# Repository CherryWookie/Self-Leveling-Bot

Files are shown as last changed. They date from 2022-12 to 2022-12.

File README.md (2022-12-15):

# Lab8 - Final Project (Self-Leveling Robot)
Michael Sell (Lab partner: Ben Schaser)

## Table of Contents:

[`Resources`](#resources)

[`Materials`](#materials)

[`Objective`](#objectiveproposal)

[`3D Printing/Laser Cutting`](#3d-printinglaser-cutting)

[`Robot Design`](#robot-design)

[`Robot Assembly`](#robot-assembly)

[`Code`](#code)

* [PID Control](#pid-control)

[`Troubleshooting`](#troubleshooting)

[`Performance`](#performance)

## Resources
#
* [Self-Levling Bot Instructional](https://www.instructables.com/Arduino-Self-Balancing-Robot-1/)
* [Self-Leveling Bot w/ Video](https://electricdiylab.com/diy-self-balancing-robot/)
* [MotorShield Instruction](https://learn.adafruit.com/adafruit-motor-shield-v2-for-arduino/using-stepper-motors)
* [Potential Wheel Option](https://www.amazon.com/90-10mm-Black-Robot-Wheels/dp/B00T3MQG7M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)
* [Accelstepper](https://github.com/adafruit/AccelStepper/blob/master/AccelStepper.cpp)
* [DC Motor that would probably work](https://www.studica.com/612rpm-6-12v-planetary-gearmotor)
* [Adafruit Motorshield Libray V_2](https://github.com/adafruit/Adafruit_Motor_Shield_V2_Library)

## Materials
#
* `Arduino UNO`

* `2 NEMA 17 Stepper Motors (42mm High Torque Hybrid Stepping Motor)`
    * [WEBPAGE for initial motors](https://www.adafruit.com/product/324)
    * [DataSheet][def]
    * [WEBPAGE for secondary motors](https://www.amazon.com/STEPPERONLINE-Stepper-Bipolar-Connector-compatible/dp/B00PNEQKC0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)

[def]: motordatasheet.jpeg

* `Adafruit Motorshield Kit`
    * [LINK TO WEBPAGE](https://www.adafruit.com/product/1438)
    * <a href="https://cdn-shop.adafruit.com/datasheets/TB6612FNG_datasheet_en_20121101.pdf">View DataSheet</a> 
    
* `Gyroscope Module`
    * [LINK TO WEBPAGE](https://www.amazon.com/HiLetgo-MPU-6050-Accelerometer-Gyroscope-Converter/dp/B00LP25V1A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)
    * Main Chip: MPU-6050
    * Power supply: 3~5V
    * Communication mode: standard IIC communication protocol
    * Chip built-in 16bit AD converter, 16bit data output
    * Gyroscopes range: +/- 250 500 1000 2000 degree/sec
    * Acceleration range: ±2 ±4 ±8 ±16g 

* `Batteries`
    * In our case: 8 AA 1.5V rechargeable batteries (TENERGY Premium 2500mAh Ni-MH Rechargeable)

* `Breadboard/wires`

* `Wheels/Tires`
    * Anything around 10cm diameter wheels should suffice. Preferably a good amount of grip for the the bot to maintain traction with various surfaces. In our case, we will be 3D Printing the wheel rims and using rubber tape to wrap around the rims for our "tires".
    * [STL FILE](wheel-rims.stl)

* `Hardware`
    * Various screws, nuts, etc. that we have yet to determine
    * Brackets for stepper motor installation
    * 4 support beams for structural integrity

* `Structure`
    * Platforms for UNO, battery, and anything else to rest on while offering the bot support. (3 in total, in our case, we will be cutting them out of a 1/4" piece of wood with a laser cutter)

## Objective/Proposal
#
Create a robot using an Arduino Uno and the above listed materials that is able to autonomously level itself without any human interaction after the bot is turned on.

`Steps to Completion:` We will be designing the robot similar to other bots listed under the [resources](#resources) section. We will be using all the components listed above with miscellaneous hardware in order to accomplish this. As for the software, we will be using a PID controller in order to control our robot. This will depend on our robot structure and the exact dimensions. We will be 3D printing the wheel rims and using the laser cutter in order to cut our platform sectionals. 

## Testing Components
#

We started by testing the stepper motors and followed the online instructions on the webpage for the motor shield. We soldered the shield and the gyroscope.

<p align="left">
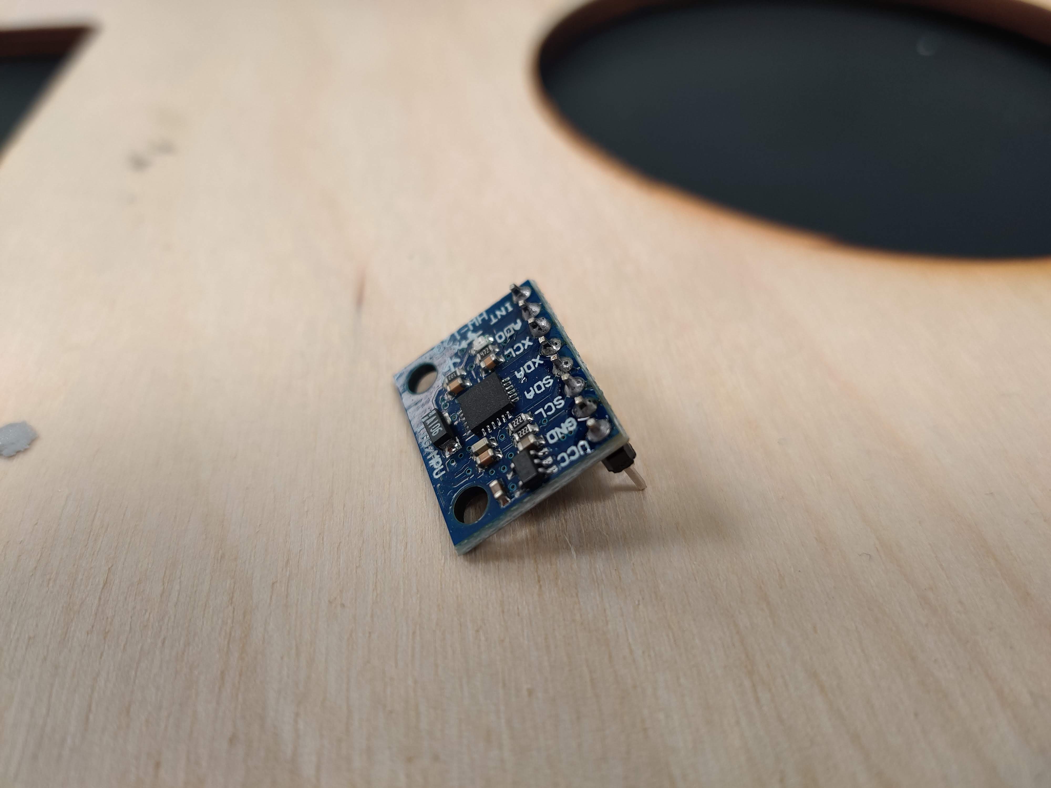
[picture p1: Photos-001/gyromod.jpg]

<align="right">
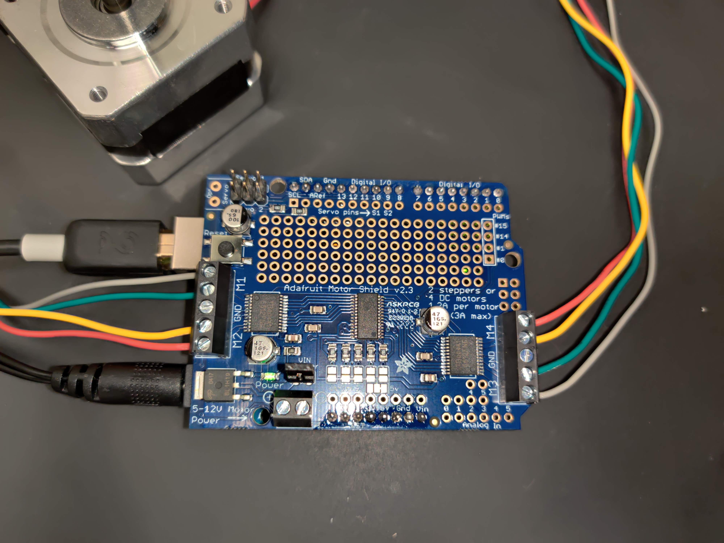
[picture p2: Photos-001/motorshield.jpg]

<align="center">
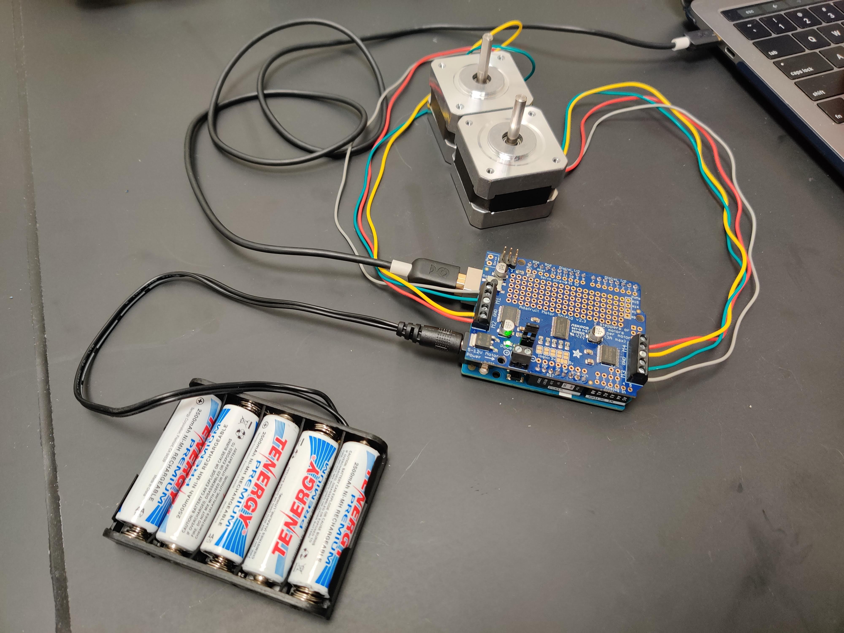
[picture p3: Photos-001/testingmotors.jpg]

</p>

We had to make sure the .h files (all the required libraries) were also in the arduino folder.

After putting the motors and the new wheels on our robot frame, we found that the motors were not making us very happy. For one, they didn't seem to be able to go fast enough. They produced very little torque and they were very jerky in motion as we have to step each one at a time instead of running them simultaneously. To remedy this, we went from the initial stepper motors and moved to our secondary stepper motors. These were rated for 2A instead of 350mA and supposedly had a higher torque at around .5NM. There is a calculation based on the weight and height of your robot to calculate how much torque is necessary for motors but we didn't do that because we were lazy. Also there weren't that many options for stepper motors so we just picked the one that could deliver the most torque without being too big. 

## 3D Printing/Laser Cutting
#

`Laser Cut thickness for red line: .072pt, Red line`

Our first test of the 3D print for the wheel rims didn't turn out very well as it printed out vertical instead of horizontal. To make it better, we switched it so that it was lying horizontal on the base plate and switched from non-soluble support material to water-soluble material so that we would end up with a cleaner product. We ended up re-printing a third time and this time opted for some larger wheels to fit our bigger robot design. 

<p align="center">
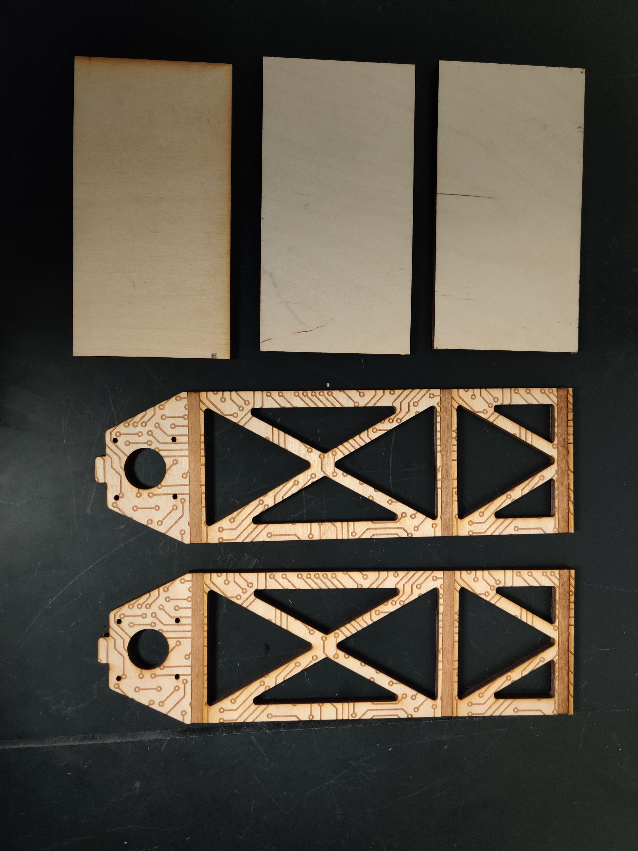
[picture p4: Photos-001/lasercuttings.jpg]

</p>

<!-- ![image](Photos-001/IMG_20221205_134104.jpg) -->
Above is the image of our laser cut components for our new design.

## Robot Design
#

Platform Dimensions: 3.5 x 7 x 1/4" (x3) (Perhaps?)
(9cm x 18cm)
8.4 cm x 16 cm

For general robot design, we started out with a rough prototype version involving a decomissioned erector set as seen below. This Mark1 was very heavy in nature due to the amount of metal used. It was also quite tall and we soon realized that we would have to look at other methods for constructing a better robot with a better weight distribution. We had thought that more weight on the top would make it easier to balance the robot, and while this may be true in theory, it ended up making the entire robot too heavy and the motors ended up not being able to move it.

<p align="left">
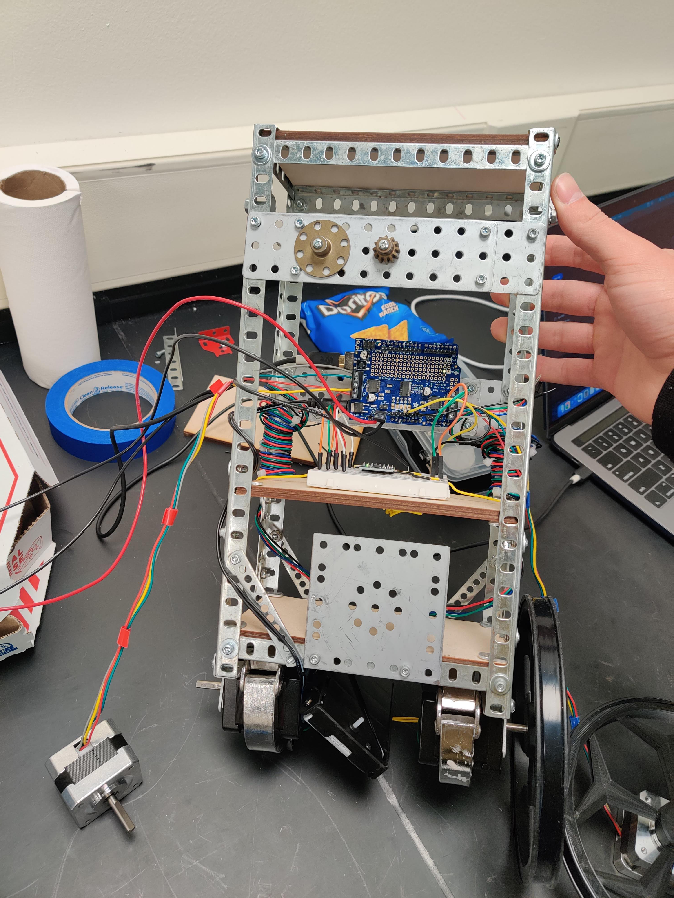
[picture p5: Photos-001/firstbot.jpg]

<align="right">
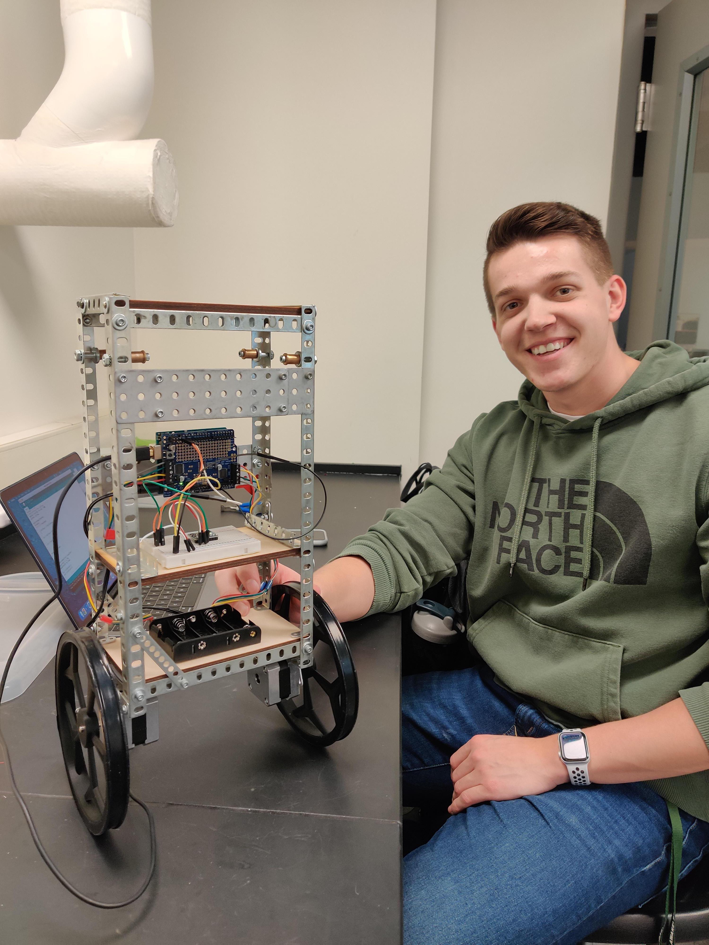
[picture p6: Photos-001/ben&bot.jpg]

</p>

Eventually, after a few days of adjusting parameters and trying different methods, we concluded the new stepper motors were still not fast enough and were not stepping in sync, causing the bot to shake violently, twist, and fall over. We then went to Dr. Kuehns laboratory and got two of his DC Planetary Gearbox motors. One of the motors he had was great with an integrated gearbox of 612RPM. This had enough speed and plenty of torque for our purposes. Unfortunately, the other gearbox was set at 60RPM and so we were unable to use them simultaneously. We purchased two more pairs of DC motors from American Science and Surplus but we quickly discovered that there was not enough torque being generated by either kind. 

We ended up completely rethinking our design as we kept running into the problem of our robot falling over too fast and the motors not having enough torque/speed to recover. We hoped that creating a chassis out of wood while making it smaller would aid in this problem. 

<p align="center">
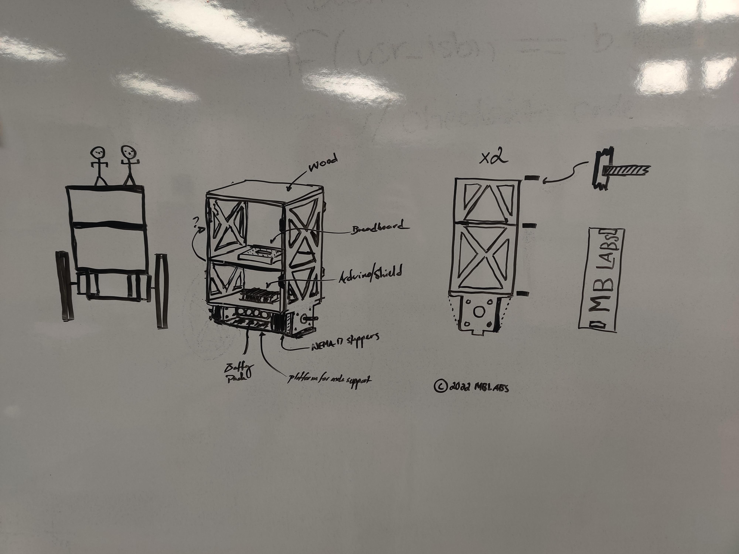
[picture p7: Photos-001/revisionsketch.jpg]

</p>

## Robot Assembly
#

`Note - Black M3 screws used to hold motors in brackets are Professor Brewsters! (Now the silver M3 screws*)`

Bonding agent used: Locktite Professional Performance Spray Adhesive (Obtained from Dr. Kuehn)

<p align="center">
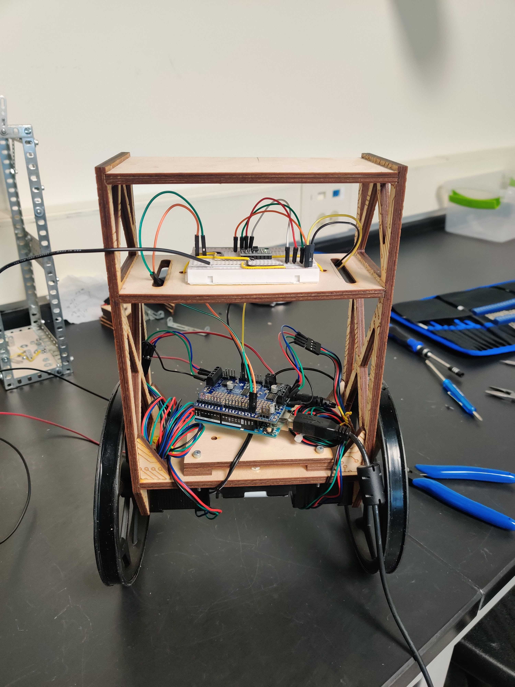
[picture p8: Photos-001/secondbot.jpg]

</p>

<p align="center">
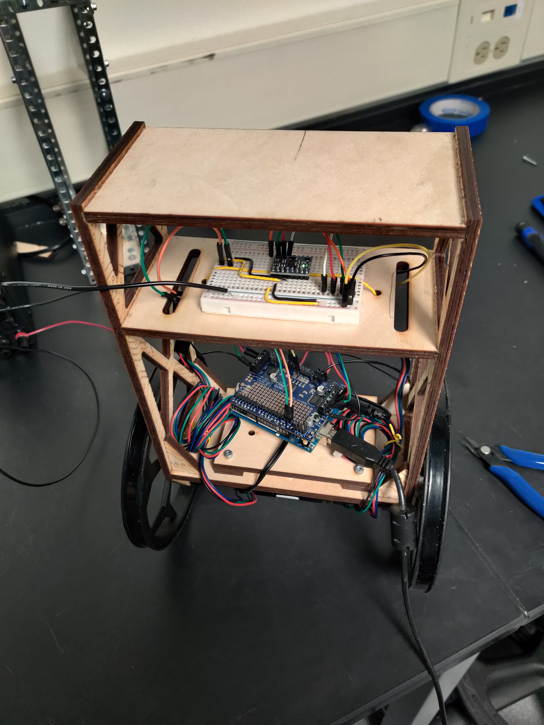
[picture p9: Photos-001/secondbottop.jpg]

</p>

After lasercutting a completely new design to accomodate our DC motors, we went back to our secondary frame and resorted to using the stepper motors. Our final design was quite good with a solid structural integrity and pleasing asthetic:

<p align="center">
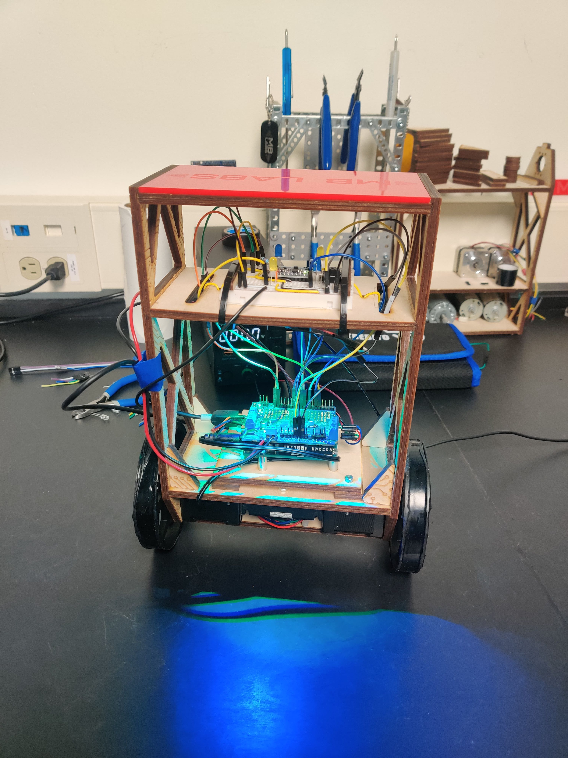
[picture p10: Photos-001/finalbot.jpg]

</p>
<p align="center">
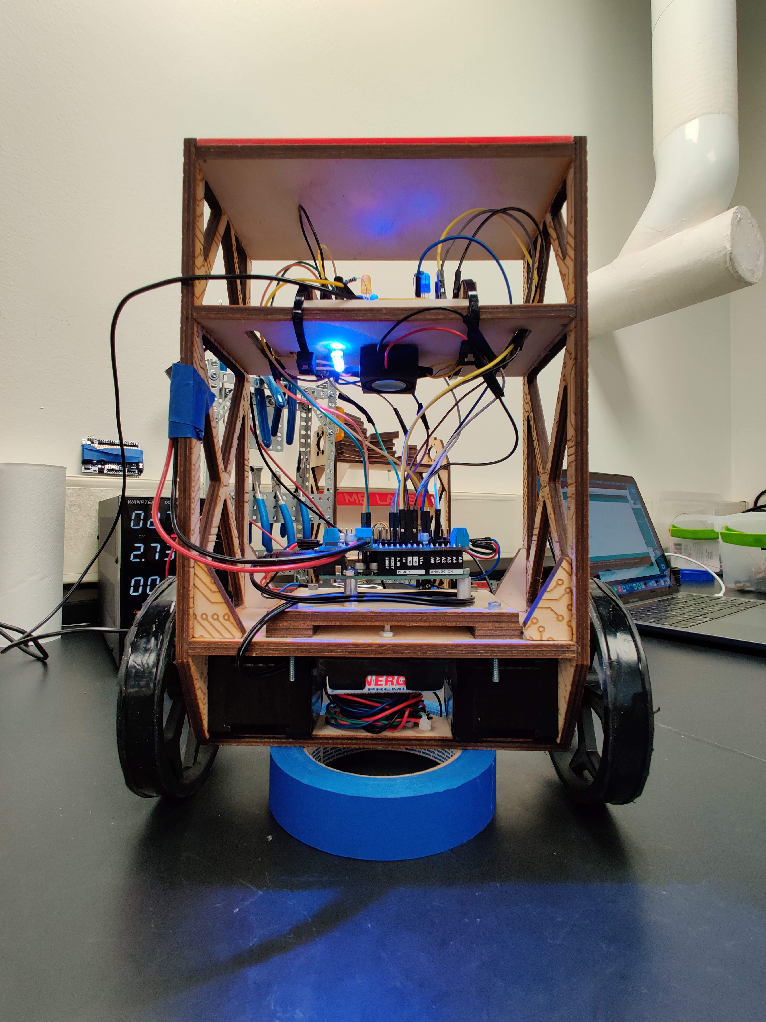
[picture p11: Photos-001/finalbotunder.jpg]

</p>

(Yes we added RGB lights and a speaker)

## Code
#

For the software, we used the instructional resources above as a rough guide of what to do. We started by using the accelerometer along with the ```atan2(x,y)``` function in order to get an angle from the acceleration. We then gathered the data from the gyroscope. The angle from the acceleration is very consistent but has to deal with gravity and acceleration in other directions while the gyroscope module has some float or accumulated error. Both of these methods have certain drawbacks, so, in order to remedy this, we applied both through a complementary filter. This allowed us to modify our output to optimize the accuracy and stability of our output angle. 

When adjusting PID parameters, we increased `Kd` until the robot just barely overshot itself when trying to correct and then turned it down slightly to just before that threshold. Secondly, we adjusted `Ki` to apply a damping of motion to the equation so that our robot would correct with out overshooting. We finally adjusted the `Ki` parameter but found that this value seemed to be detrimental to the functionality of our stepper motors and so we kept this value << 1

With adjusting the PID control, we found it was much easier to adjust the PID parameters using potentiometers in real-time instead of guessing a value and uploading the code hundreds of times. We used a simple 10k Ohm pot to tun ours. 

<details>
<summary> 
<font size="5">Early Iteration of Code </font>
</Summary>
<br>
<font size="1">

```C++
// Michael Sell and Ben Schaser
// Full code (early version):

#include <Wire.h>
#include <Adafruit_MPU6050.h>
#include <Adafruit_Sensor.h>
#include <Adafruit_MotorShield.h>
#include "utility/Adafruit_MS_PWMServoDriver.h"

Adafruit_MPU6050 mpu;
Adafruit_MotorShield AFMS = Adafruit_MotorShield();
Adafruit_StepperMotor *leftMotor = AFMS.getStepper(600, 2);
Adafruit_StepperMotor *rightMotor = AFMS.getStepper(600, 1);

// Angle of Inclination
double accX, accZ;
double accAngle;
int gyroY, gyroRate;
double gyroAngle = 0;
double gyroAngleNext = 0;
double gyroAnglePrev = 0;
unsigned long currTime, prevTime = 0;
double loopTime;
double currentAngle = 0;
double prevAngle = 0;
double prevPrevAngle = 0;
double nextAngle = 0;
double tau = 0.7;
double dt = 0.004;
double alpha = tau / (tau + dt);

// PID Constants
double Kp = 0.0;
double Ki = 0.0;
double Kd = 0.0;

double targetAngle = 0;
double difference = 0;
double prevDif = 0;
double difSum = 0;
double motorSpeed = 0;
double RtoD = 57.2957795131;

void setup() {
  Serial.begin(9600);
  mpu.begin();

  // set accelerometer range to +-8G
  mpu.setAccelerometerRange(MPU6050_RANGE_8_G);

  // set gyro range to +- 500 deg/s
  mpu.setGyroRange(MPU6050_RANGE_500_DEG);

  // set filter bandwidth to 21 Hz
  mpu.setFilterBandwidth(MPU6050_BAND_21_HZ);

  //  mpu.setXAccelOffset(315);
  //  mpu.setYAccelOffset(993);
  //  mpu.setZAccelOffset(415);
  //  mpu.setXGyroOffset(93);
  //  mpu.setYGyroOffset(-23);
  //  mpu.setZGyroOffset(-11);

  AFMS.begin();
  TWBR = ((F_CPU/400000l) - 16)/2; // Change the i2c clock speed to 400KHz
}

void loop() {
  currTime = millis();
  //  Serial.println(currTime - prevTime);
  loopTime = (currTime - prevTime);
  loopTime = loopTime / 1000;
  prevTime = currTime;
  
  getCurrentAngle(loopTime);
  Serial.println(currentAngle);
  calcSpeed();
//  Serial.println(motorSpeed);
  //
//  if ((currentAngle + prevAngle + prevPrevAngle) / 3 < -1.0) {
//    leftMotor->setSpeed(motorSpeed);
//    rightMotor->setSpeed(motorSpeed);
//    leftMotor->step(1, BACKWARD, DOUBLE);
//    rightMotor->step(1, FORWARD, DOUBLE);
//  }
//  else if ((currentAngle + prevAngle + prevPrevAngle) / 3 > 1.0) {
//    leftMotor->setSpeed(motorSpeed);
//    rightMotor->setSpeed(motorSpeed);
//    leftMotor->step(1, FORWARD, DOUBLE);
//    rightMotor->step(1, BACKWARD, DOUBLE);
//  }
  prevPrevAngle = prevAngle;
  prevAngle = currentAngle;
}

void getCurrentAngle(double elapsedTime) {
  sensors_event_t a, g, temp;
  mpu.getEvent(&a, &g, &temp);

  accZ = a.acceleration.z;
  accX = a.acceleration.x;
//  Serial.print(accX);
//  Serial.print("  ");
//  Serial.print(accZ);
//  Serial.print('\n');

  accAngle = atan2(accX, accZ) * RtoD;

  gyroY = g.gyro.y;

  gyroRate = map(gyroY, -32768, 32767, -250, 250);
  gyroAngle = gyroAngle + (float)gyroRate * elapsedTime;
  currentAngle = tau * (prevAngle + gyroAngle*dt) + (1 - tau) * accAngle;
//  Serial.println(accAngle);

//  alternative formula - leapfrog method :)
//  gyroAngleNext = (gyroAnglePrev + gyroAngle) / 2 + accAngle*elapsedTime;
//  nextAngle = currentAngle;

}
void calcSpeed() {
  difference = currentAngle - targetAngle;
  difSum += difference;
  difSum = constrain(difSum, -300, 300);
  motorSpeed = Kp * difference + Ki * difSum * loopTime + Kd * (difference - prevDif) / loopTime;
  prevDif = difference;
}
```</font>
<details>

### PID Control

Our PID Controller (Proportional, Integral, Derivative), is calculated in the following function, where `Kp` is the proportional parameter, `Ki` is the integral parameter, and `Kd` is our derivative parameter. This was used to calculate our `motorspeed` value in order to adjust the speed for the smoothest possible curve to a balanced state.

<font size="1">

```C++
void calcSpeed(double angle) {
  error = targetAngle - angle;
  errSum += error * loopTime;
  errSum = constrain(errSum, -300, 300);
  motorSpeed = Kp * error + Ki * errSum + Kd * (error - prevError) / loopTime;
  prevError = error;
}
```

</font>
</details>

<details>
<summary> 
<font size="5"> Final Code </font>
 </Summary>
<br>
<font size="1">

```C++
// Michael S. & Ben S. 12/13/22
// Final code for SLB
   
#include <Wire.h>
#include <Adafruit_MPU6050.h>
#include <Adafruit_Sensor.h>
#include <Adafruit_MotorShield.h>
#include <AccelStepper.h>
#include <Kalman.h>

Adafruit_MPU6050 mpu;
Adafruit_MotorShield AFMS = Adafruit_MotorShield();
Adafruit_StepperMotor *leftMotor = AFMS.getStepper(200, 2);
Adafruit_StepperMotor *rightMotor = AFMS.getStepper(200, 1);
void forwardstep1() {
  leftMotor->onestep(BACKWARD, DOUBLE);
  rightMotor->onestep(FORWARD, DOUBLE);
}
void backwardstep1() {
  leftMotor->onestep(FORWARD, DOUBLE);
  rightMotor->onestep(BACKWARD, DOUBLE);
}
AccelStepper Astepper(forwardstep1, backwardstep1); // use functions to step

// Angle of Inclination
double accX, accZ;
double accAngle;
int gyroY, gyroRate;
double gyroAngle = 0;
double gyroAngleNext = 0;
double gyroAnglePrev = 0;
unsigned long currTime, prevTime = 0;
double loopTime = 0.0;
double currentAngle = 0;
double prevAngle = 0;
double tau = 0.7;
double alpha = tau / (tau + loopTime);

Kalman kalmanY;
double pitch = 0.0;
double kalAngleY = 0.0;
double gyroYrate = 0.0;
//double prevAngle = 0.0;
double prevPrevAngle = 0.0;

// PID Constants
double Kp = 39.5;
double Ki = 2.2;
double Kd = 0.11;
int inKp = 0;

double targetAngle = 0.0;
double minError = -15.0;
double maxError = 15.0;
double error = 0;
double prevError = 0;
double errSum = 0;
double motorSpeed = 0;
double prevMotorSpeed = 0;
double motorSpeedAvg = 0;

double motorCutoff = 1.0;
double angleThreshold = 0.9;
bool active = false;
int buttonState = 0;

int rDir = 1;
int gDir = 1;
int bDir = 1;
int rVal = 0;
int gVal = 120;
int bVal = 254;

void setup() {
  Wire.begin();
  mpu.begin();

  // set accelerometer range to +-8G
  mpu.setAccelerometerRange(MPU6050_RANGE_8_G);

  // set gyro range to +- 500 deg/s
  mpu.setGyroRange(MPU6050_RANGE_500_DEG);

  // set filter bandwidth to 21 Hz
  mpu.setFilterBandwidth(MPU6050_BAND_21_HZ);

  AFMS.begin();
  leftMotor->setSpeed(1);
  rightMotor->setSpeed(1);
  TWBR = ((F_CPU/400000l) - 16) / 2;

  pinMode(8, INPUT); // btn
  pinMode(3, OUTPUT);
  pinMode(4, OUTPUT);
  pinMode(5, OUTPUT);
  pinMode(6, OUTPUT);
  pinMode(9, OUTPUT);
  pinMode(10, OUTPUT);
  pinMode(11, OUTPUT);
  pinMode(12, OUTPUT);
  startPing();
}

void loop() {
  buttonState = digitalRead(8);
  rVal = rVal + rDir;
  gVal = gVal + gDir;
  bVal = bVal + bDir;

  // for each color, change direction if reached 0 or 255
  if (rVal >= 255 || rVal <= 0) {
    rDir = rDir * -1;
  }

  if (gVal >= 255 || gVal <= 0) {
    gDir = gDir * -1;
  }

  if (bVal >= 255 || bVal <= 0) {
    bDir = bDir * -1;
  }
  RGB_color(rVal, gVal, bVal);
  if (buttonState == 1) {
    active = !active;
    delay(200);
  }
  
  if (active) {
    digitalWrite(5, HIGH);
    digitalWrite(4, HIGH);
    _main();
  }
  else {
    leftMotor->release();
    rightMotor->release();
    digitalWrite(5, LOW);
    digitalWrite(4, LOW);
  }
}
void _main() {
  currTime = millis();
  loopTime = (currTime - prevTime);
  loopTime = loopTime / 1000;
  prevTime = currTime;  
  
  getCurrentAngle(loopTime);
  calcSpeed(currentAngle);
  motorSpeed = constrain(motorSpeed, -500, 500);

  if(currentAngle > targetAngle + angleThreshold || currentAngle < targetAngle - angleThreshold) {
    drive();
  }
  
  prevAngle = currentAngle;
  prevMotorSpeed = motorSpeed;
  prevPrevAngle = prevAngle;
  prevAngle = currentAngle;
}

void getCurrentAngle(double elapsedTime) {
  sensors_event_t a, g, temp;
  mpu.getEvent(&a, &g, &temp);

//  Kalman Filter
  gyroY = g.gyro.y;
  gyroYrate = g.gyro.y / 131.0;
  pitch = atan2(-a.acceleration.x, a.acceleration.z) * RAD_TO_DEG;
  kalAngleY = kalmanY.getAngle(pitch, gyroYrate, loopTime);
  currentAngle = kalAngleY + 3.0;
}

void calcSpeed(double angle) {
  error = targetAngle - angle;
  errSum += error * loopTime;
  errSum = constrain(errSum, -300, 300);
  motorSpeed = Kp * error + Ki * errSum + Kd * (error - prevError) / loopTime;
  prevError = error;
}

void drive() {
  if (motorSpeed > motorCutoff  || motorSpeed < -motorCutoff) {
    Astepper.setSpeed(motorSpeed);
  }
  Astepper.runSpeed();
}

void startPing() {
  tone(7, 500, 600);
  delay(600);
  tone(7, 750, 100);
  delay(100);
  tone(7, 1000, 50);
  delay(50);
  tone(7, 1500, 50);
  delay(50);
  tone(7, 2000, 50);
  delay(50);
  tone(7, 1500, 50);
  delay(50);
  tone(7, 1000, 100);
  delay(100);
  tone(7, 10, 50);
  delay(50);
}

void RGB_color(int red, int green, int blue) {
  analogWrite(11, red);
  analogWrite(10, green);
  analogWrite(9, blue);
}

```
</font>
</details>

____

## PID Control

Our PID Controller (Proportional, Integral, Derivative), is calculated in the following function, where `Kp` is the proportional parameter, `Ki` is the integral parameter, and `Kd` is our derivative parameter. This was used to calculate our `motorspeed` value in order to adjust the speed for the smoothest possible curve to a balanced state.

<font size="1">

```C++
void calcSpeed(double angle) {
  error = targetAngle - angle;
  errSum += error * loopTime;
  errSum = constrain(errSum, -300, 300);
  motorSpeed = Kp * error + Ki * errSum + Kd * (error - prevError) / loopTime;
  prevError = error;
}
```

</font>

## Troubleshooting
#
Where to start?

This project was objectively about 90% troubleshooting, whether physical design troubleshooting or software issues. Our biggest struggle was finding motors that worked for us and figuring out how to use them to their fullest potential. Our initial stepper motors were underpowered for our purposes but the second motors should have had enough power for our purposes. We were unable to get our motors to spin as fast as we needed for a long time. Below is a list of things that we did in order to increase our motorspeed and efficiency:

1. Increase the I2C Bus Speed between the arduino and Adafruit motorshield with the following command:
```C++
TWBR = ((F_CPU/400000l) - 16) / 2; // This increases the clock speed to 4KHz instead of 1KHz. Make sure to place this line in the setup() loop
```
2. Use the `AccelStepper` library for more integrated simultaneous motor dynamics.

3. Find the maximum RPM of the motor with trial and error and don't go over that speed.

4. Supply enough current to the motors.

5. Although we didn't do this, we believe that using a common H-bridge motor speed controller as apposed to the Adafruit motorshield would allow for faster motor speeds due to the constraning 1.2A max limit for the motorshield. Because of this, we were unable to push the stepper motors to their 2A (each) limit.

6. *IMPORTANT:* Delete/comment out ALL `serial` commands. (including `serial.begin()`, `serial.print()` etc.) This slows down the loop speed dramatically and reduces the speed of the motors by a significant margin. 

Another area of troubleshooting was the software. We were unable to reliably get angular readings at first until we realized that the gyroscope module was accumulating error and was throwing the system off. We remedied this through some simple tweaks with our complimentary filter and ended up switching completely to a Kalman filter for a more stable angle reading.

Along with this, we were getting some very wild oscillations in our motorspeed when our angles were small, giving rise to a very violent shaking motion when the robot was on. To fix this problem, we found out that it was potentially because of our PID parameters being set too high. After turning down the parameters and multiplying the motorspeed output by an arbitrary integer amount to increase the speed, we started to obtain a smoother rolling bot. 

## Performance
#

Performace was relative for our robot, although it didn't perform completely sans human interference like we had hoped. We had a few guesses as to why this was the case. First, the current limiting motorshield wasn't helping our case. Second, the motors themselves perhaps weren't the best options for our purposes. Some higher-quality DC gearbox motors might have been better. Finally, we noticed that the robot was having a hard time balancing due to the three wires connecting it to the power supply. We didn't have sufficient battery power to run the motors with our 5 AA batteries so it was a neccessary component for running our robot. Because of this, the balance for the robot was extremely variable in whichever direction the wires were pulling. Because of this, it made it almost impossible to fine tune our PID parameters to adjust it for the perfect balance. An higher capacity battery pack would be a necessity for something like this in future iterations. That being said, our Mk.3 bot was able to self balance with minimal human interaction and the proof of concept was definitelly there. 



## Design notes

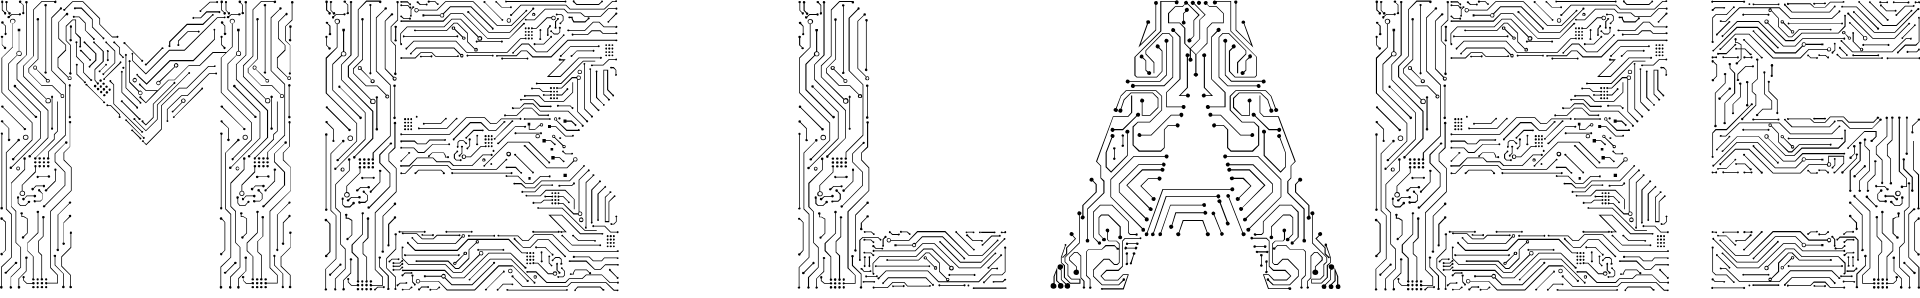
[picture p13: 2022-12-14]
Photos-001/text-1670191978055.png

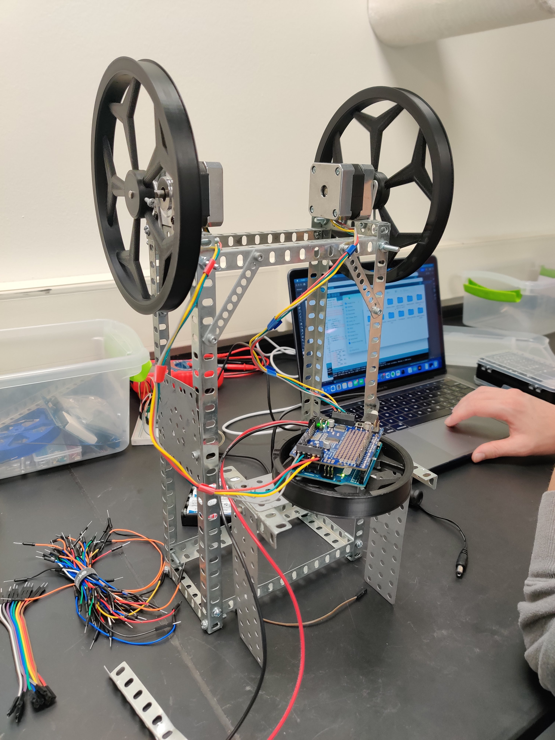
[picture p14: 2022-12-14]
Photos-001/initialwheeltest.jpg

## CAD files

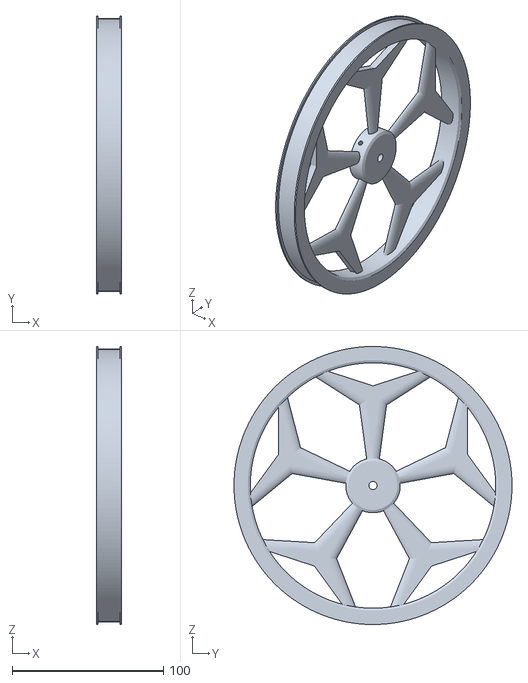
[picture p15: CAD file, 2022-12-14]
big-wheels.stl
16.3 x 183.6 x 183.6

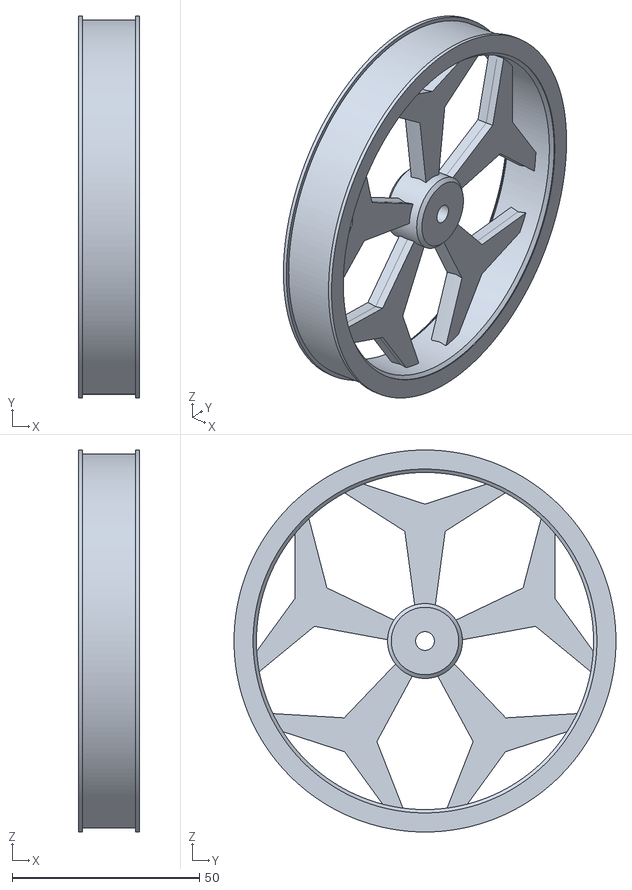
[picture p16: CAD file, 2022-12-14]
wheel-rims.stl
16.3 x 102.0 x 102.0

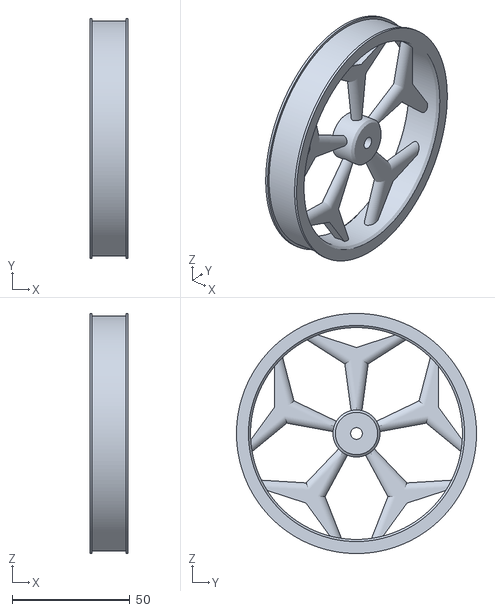
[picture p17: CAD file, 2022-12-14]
wheel-rims-smooth.stl
16.3 x 102.0 x 102.0

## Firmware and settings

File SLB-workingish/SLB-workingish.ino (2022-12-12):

#include <Wire.h>
#include <Adafruit_MPU6050.h>
#include <Adafruit_Sensor.h>
#include <Adafruit_MotorShield.h>
#include <AccelStepper.h>
#include <Kalman.h>
//#include "utility/Adafruit_MS_PWMServoDriver.h"

Adafruit_MPU6050 mpu;
Adafruit_MotorShield AFMS = Adafruit_MotorShield();
Adafruit_StepperMotor *leftMotor = AFMS.getStepper(200, 2);
Adafruit_StepperMotor *rightMotor = AFMS.getStepper(200, 1);
void forwardstep1() {
  leftMotor->onestep(BACKWARD, DOUBLE);
  rightMotor->onestep(FORWARD, DOUBLE);
}
void backwardstep1() {
  leftMotor->onestep(FORWARD, DOUBLE);
  rightMotor->onestep(BACKWARD, DOUBLE);
}
AccelStepper Astepper(forwardstep1, backwardstep1); // use functions to step

// Angle of Inclination
double accX, accZ;
double accAngle;
int gyroY, gyroRate;
double gyroAngle = 0;
double gyroAngleNext = 0;
double gyroAnglePrev = 0;
unsigned long currTime, prevTime = 0;
double loopTime = 0.0;
double currentAngle = 0;
double prevAngle = 0;
double tau = 0.7;
//double dt = 0.0;
double alpha = tau / (tau + loopTime);

Kalman kalmanY;
double pitch = 0.0;
double kalAngleY = 0.0;
double gyroYrate = 0.0;

// PID Constants - Adjust as neccessary: Start with Kp, then Kd, then Ki for best results.
double Kp = 3.6;
double Ki = 0.00;
double Kd = 0.000;

double targetAngle = 0;
double minError = -11.5;
double maxError = 20.5;
double error = 0;
double prevError = 0;
double errSum = 0;
double motorSpeed = 0;
double prevMotorSpeed = 0;
double prevPrevMotorSpeed = 0;
double motorSpeedAvg = 0;
double motorSpeedConv = 0;
double RtoD = 57.2957795131;
double motorCutoff = 2.0;
bool active = false;
int buttonState = 0;

void setup() {
//  Serial.begin(9600);  // Comment out to decrease loop delay as well as any other serial commands
  mpu.begin();

  // set accelerometer range to +-8G
  mpu.setAccelerometerRange(MPU6050_RANGE_8_G);

  // set gyro range to +- 500 deg/s
  mpu.setGyroRange(MPU6050_RANGE_500_DEG);

  // set filter bandwidth to 21 Hz
  mpu.setFilterBandwidth(MPU6050_BAND_21_HZ);

  //  mpu.setXAccelOffset(315);
  //  mpu.setYAccelOffset(993);
  //  mpu.setZAccelOffset(415);
  //  mpu.setXGyroOffset(93);
  //  mpu.setYGyroOffset(-23);
  //  mpu.setZGyroOffset(-11);

  AFMS.begin();
  leftMotor->setSpeed(1);
  rightMotor->setSpeed(1);
  TWBR = ((F_CPU/400000l) - 16) / 2;

  pinMode(8, INPUT); // btn
}

void loop() {
//   buttonState = digitalRead(8);
// //  Serial.println(buttonState);
//   if (buttonState == 1) {
//     active = !active;
//     delay(200);
//   }
  
//   if (active) {
//     _main();
//   }
 _main();
}
void _main() {
  currTime = millis();
//  Serial.println(currTime - prevTime);
  loopTime = (currTime - prevTime);
//  Serial.println(loopTime);
  loopTime = loopTime / 1000;
  prevTime = currTime;
//  dt = loopTime;
  
  
  getCurrentAngle(loopTime);
  calcSpeed(currentAngle);
  motorSpeed = constrain(motorSpeed, -500, 500);
//  motorSpeed = map(motorSpeed, -1000, 1000, -500, 500);
//  Serial.println(motorSpeed);
//  motorSpeedConv = map(abs(motorSpeed), 0, 150, 50, 255);
  if(currentAngle > 1.4 || currentAngle < -1.4) {
  drive();
  }
  
  prevAngle = currentAngle;
//  prevPrevMotorSpeed = prevMotorSpeed;
  prevMotorSpeed = motorSpeed;
//  Serial.print(currentAngle);
//  Serial.print(' ');
//  Serial.println();
//  Serial.print(targetAngle);
//  Serial.print(' ');
}

void getCurrentAngle(double elapsedTime) {
  sensors_event_t a, g, temp;
  mpu.getEvent(&a, &g, &temp);

  accZ = a.acceleration.z;
  accX = a.acceleration.x;
//  Serial.print(accX);
//  Serial.print("  ");
//  Serial.print(accZ);
//  Serial.print('\n');

  accAngle = atan2(accX, accZ) * RtoD;

  gyroY = g.gyro.y;

//  Complementary Filter
//  gyroRate = map(gyroY, -32768, 32767, -250, 250);
//  gyroAngle = gyroAngle + (float)gyroRate * elapsedTime;
//  currentAngle = tau * (prevAngle + gyroAngle*loopTime) + (1 - tau) * accAngle;

//  Kalman Filter
  gyroYrate = g.gyro.y / 131.0;
  pitch = atan2(-a.acceleration.x, a.acceleration.z) * RAD_TO_DEG;

  kalAngleY = kalmanY.getAngle(pitch, gyroYrate, loopTime);
  currentAngle = kalAngleY;
  currentAngle += 4.1;
  // Serial.print(currentAngle);
}
void calcSpeed(double angle) {
  error = targetAngle - angle;
  errSum += error * loopTime;
  errSum = constrain(errSum, -300, 300);
  motorSpeed = Kp * error + Ki * errSum + Kd * (error - prevError) / loopTime;
  motorSpeed *=10;
  prevError = error;  
//  motorSpeedAvg = 0.2 * prevMotorSpeed + 0.8 * motorSpeed;
//  Serial.println(motorSpeed);
}
void drive() {
  if (motorSpeed > motorCutoff  || motorSpeed < -motorCutoff) {
    Astepper.setSpeed(motorSpeed);
    Astepper.runSpeed();
  }
//  else {
//    leftMotor->release();
//    rightMotor->release();
//  }
  
}
